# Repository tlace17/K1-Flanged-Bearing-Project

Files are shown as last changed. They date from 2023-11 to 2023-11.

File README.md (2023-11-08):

# K1-Flanged-Bearing-Project
D3D community based K1 and K1 Max Gantry Mod

<table>
  <tr>
   <td colspan="4" >



<p>
The K1 Flanged Bearing Project was developed within the <a href="https://github.com/D3vil-Design">D3vil Design (D3D)</a> community as an effort to further advance the precision and speed of the K1 and K1 Max 3D printers from Creality. Inspired by the work of Derrick Darrell and Omran Al Sayed from the D3D Dev team and their early gantry improvements to the stock setup of the K1 and K1 Max.
<p>
This project aims to replace all idlers on the gantry with the flanged bearing variety commonly seen on Voron Design printers over the last 5 years. These provide improved belt alignment and quieter operation at faster speeds. These bearings alongside some changes to the gantry idler locations provide a proper belt path for standard corexy operation.
<p>
<strong>Included in this document are installation manuals for all 3 types of components within the gantry upgrades and a Bill of Materials for needed parts.</strong>

<h1>Print Settings:</h1>
<p>
<strong>Material:</strong> ABS or better
<p>
<strong>Infill:</strong> Gyroid 20% or more
<p>
<strong>Layer Height:</strong> 0.2mm maximum, 0.12mm preferred
<p>
<strong>Wall Loops:</strong> 2 minimum, 3-4 preferred
<p>
<strong>Top and Bottom Layers:</strong> 4 minimum, 5 preferred
<p>
<strong>Supports:</strong> Needed (Normal is better than tree for most parts, be careful removing supports)
<p>
<h1>Install Manuals:</h1>

<p>
<a href="https://docs.google.com/document/u/0/d/1f634rc0oCE0zsnbUDskOYYNibStS-vbxrUdUEM-Z9eU/edit">Tensioner Assembly</a>
<p>
<a href="https://docs.google.com/document/u/0/d/1OAUH_pnmw2NlV73cRtI84WbWtc6erK8xQ9Lfi24KxoA/edit">Motor Mount Assembly</a>
<p>
<a href="https://docs.google.com/document/u/0/d/13FziAajVrfHMsXNUPVWEJ_OhXhJzXreVzjQ5gYJWXsE/edit">XY Joint Assembly</a>
<h1>BOM</h1>

   </td>
  </tr>
  <tr>
   <td>Count
   </td>
   <td>Item
   </td>
   <td>Amazon
   </td>
   <td>AliExpress
   </td>
  </tr>
  <tr>
   <td>2
   </td>
   <td>M3x20 and/or M3x25 SHCS
   </td>
   <td><a href="https://www.amazon.com/iExcell-Stainless-Metric-Socket-Washers/dp/B0812TYT5L/">https://www.amazon.com/iExcell-Stainless-Metric-Socket-Washers/dp/B0812TYT5L/</a>
   </td>
   <td><a href="https://www.aliexpress.us/item/2251832670224681.html">https://www.aliexpress.us/item/2251832670224681.html</a> <strong>(Select M3)</strong>
   </td>
  </tr>
  <tr>
   <td>6
   </td>
   <td>M3x25 FHCS
   </td>
   <td><a href="https://www.amazon.com/gp/product/B09BRDLF6N/">https://www.amazon.com/gp/product/B09BRDLF6N/</a>
   </td>
   <td><a href="https://www.aliexpress.us/item/3256801607716281.html">https://www.aliexpress.us/item/3256801607716281.html</a> <strong>(Select M3x25)</strong>
   </td>
  </tr>
  <tr>
   <td>18
   </td>
   <td>M3 Heat Set Inserts
   </td>
   <td><a href="https://www.amazon.com/gp/product/B08K1BVGN9">https://www.amazon.com/gp/product/B08K1BVGN9</a>
   </td>
   <td><a href="https://www.aliexpress.us/item/3256804437259312.html">https://www.aliexpress.us/item/3256804437259312.html</a> <strong>(Select M3xOD4.6 +5.5mm length)</strong>
   </td>
  </tr>
  <tr>
   <td>6
   </td>
   <td>M3 Thin Square Nut
   </td>
   <td><a href="https://www.amazon.com/gp/product/B0BD2N9KTV/">https://www.amazon.com/gp/product/B0BD2N9KTV/</a>
   </td>
   <td><a href="https://www.aliexpress.us/item/3256804297147723.html">https://www.aliexpress.us/item/3256804297147723.html</a> <strong>(Select M3)</strong>
   </td>
  </tr>
  <tr>
   <td>24
   </td>
   <td>F623zz Bearings
   </td>
   <td><a href="https://www.amazon.com/dp/B0CGXF7JMP">https://www.amazon.com/dp/B0CGXF7JMP</a>
   </td>
   <td><a href="https://www.aliexpress.us/item/2251832201217481.html">https://www.aliexpress.us/item/2251832201217481.html</a><strong> (Select F623ZZ)</strong>
   </td>
  </tr>
  <tr>
   <td>
   </td>
   <td>or
   </td>
   <td>
   </td>
   <td>
   </td>
  </tr>
  <tr>
   <td>24
   </td>
   <td>F623 2RS Bearings
   </td>
   <td><a href="https://www.amazon.com/dp/B0CGXFY2BX/">https://www.amazon.com/dp/B0CGXFY2BX/</a>
   </td>
   <td><a href="https://www.aliexpress.us/item/2255800912664897.html">https://www.aliexpress.us/item/2255800912664897.html</a>
   </td>
  </tr>
  <tr>
   <td>4
   </td>
   <td>M3x40 FHCS
   </td>
   <td><a href="https://www.amazon.com/gp/product/B09BRDLF6N/">https://www.amazon.com/gp/product/B09BRDLF6N/</a>
   </td>
   <td><a href="https://www.aliexpress.us/item/3256801607716281.html">https://www.aliexpress.us/item/3256801607716281.html</a> <strong>(Select M3x40)</strong>
   </td>
  </tr>
  <tr>
   <td>8
   </td>
   <td>M5x5mm Set Screw
   </td>
   <td><a href="https://www.amazon.com/gp/product/B0BXNL9S4D/">https://www.amazon.com/gp/product/B0BXNL9S4D/</a>
   </td>
   <td><a href="https://www.aliexpress.us/item/3256805120444593.html">https://www.aliexpress.us/item/3256805120444593.html</a>
   </td>
  </tr>
  <tr>
   <td>24
   </td>
   <td>M3 1mm Spacer
   </td>
   <td><a href="https://www.amazon.com/gp/product/B01N7CJMVL/">https://www.amazon.com/gp/product/B01N7CJMVL/</a>
   </td>
   <td><a href="https://www.aliexpress.us/item/3256802114850018.html">https://www.aliexpress.us/item/3256802114850018.html</a> <strong>(Select M3x6xThick + 1mm thick)</strong>
   </td>
  </tr>
  <tr>
   <td>16
   </td>
   <td>M3x8 FHCS
   </td>
   <td><a href="https://www.amazon.com/gp/product/B09BRDLF6N/">https://www.amazon.com/gp/product/B09BRDLF6N/</a>
   </td>
   <td><a href="https://www.aliexpress.us/item/3256801607716281.html">https://www.aliexpress.us/item/3256801607716281.html</a> <strong>(Select M3x8)</strong>
   </td>
  </tr>
    <tr>
   <td>12
   </td>
   <td>M3x0.5 Spacer/Washer
   </td>
   <td><a href="https://www.amazon.com/gp/product/B09BRDLF6N/">https://www.amazon.com/gp/product/B09BRDLF6N/</a>
   </td>
   <td><a href="https://www.aliexpress.us/item/3256802114850018.html">https://www.aliexpress.us/item/3256802114850018.html</a> <strong>(Select M3x6xThick + 0.5mm thick)</strong>
   </td>
  </tr>
</table>

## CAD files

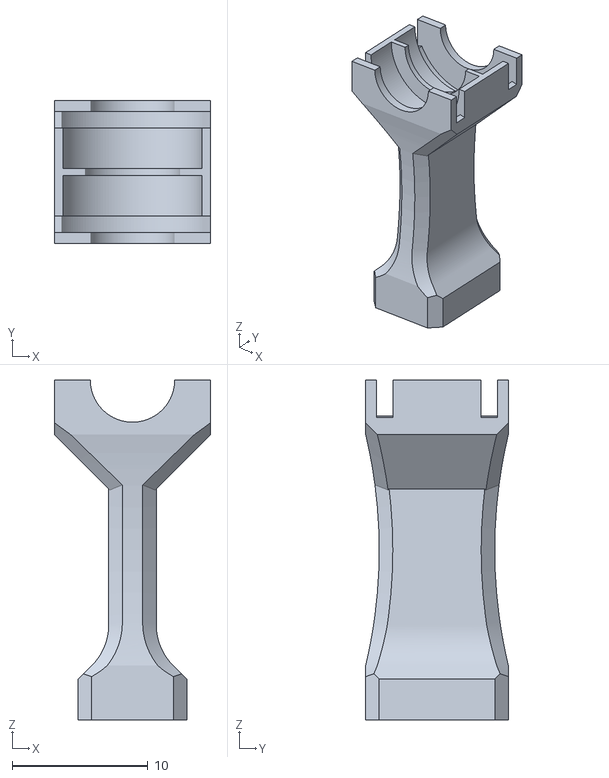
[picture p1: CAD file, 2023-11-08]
Bearing Stack Tool.stl
11.5 x 10.5 x 25.0

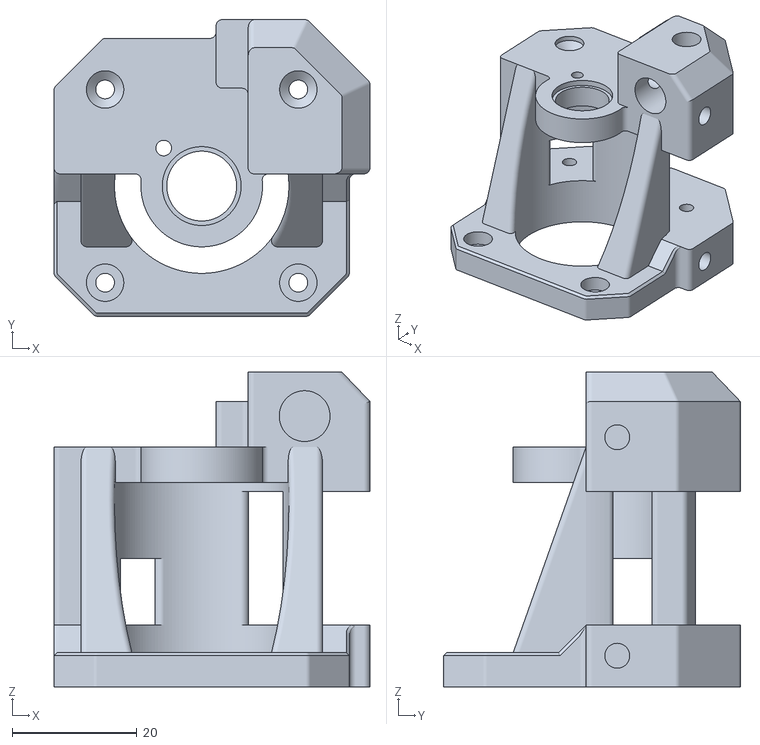
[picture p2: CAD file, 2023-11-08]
Gantry STLs/Right Stepper Mount.stl
50.7 x 47.6 x 50.5

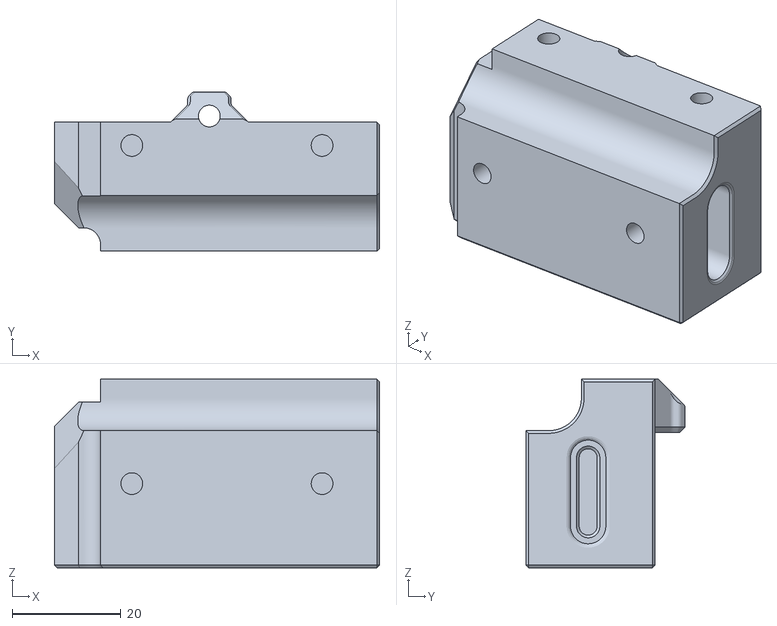
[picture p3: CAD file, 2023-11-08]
Gantry STLs/Left Tensioner Housing.stl
59.9 x 29.4 x 34.8

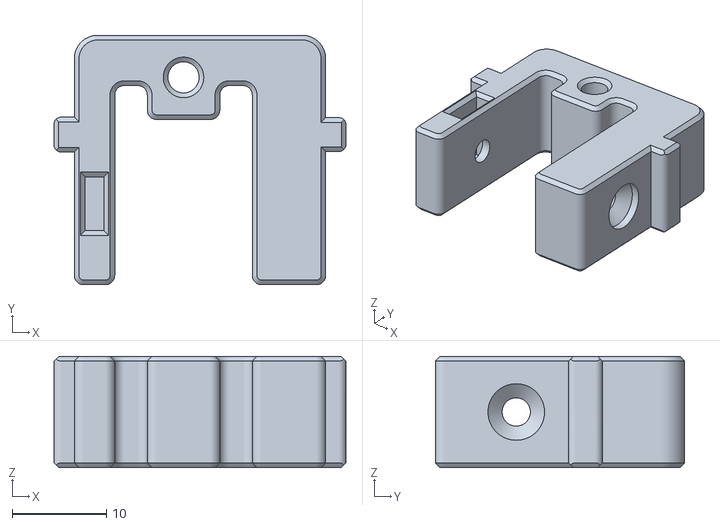
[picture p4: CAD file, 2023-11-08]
Gantry STLs/Left Tensioner.stl
31.0 x 26.5 x 11.8

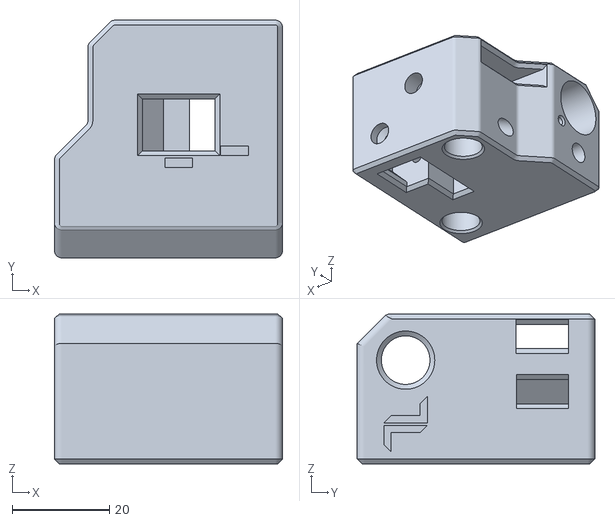
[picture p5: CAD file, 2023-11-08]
Gantry STLs/Right XY Joint.stl
47.0 x 49.0 x 30.9

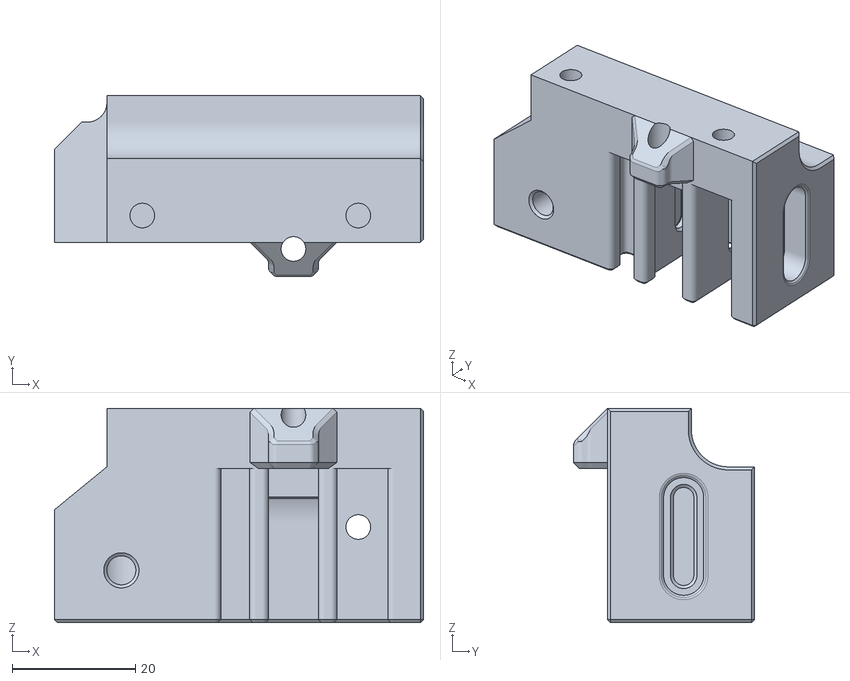
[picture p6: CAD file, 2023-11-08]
Gantry STLs/Right Tensioner Housing.stl
59.9 x 29.4 x 34.8

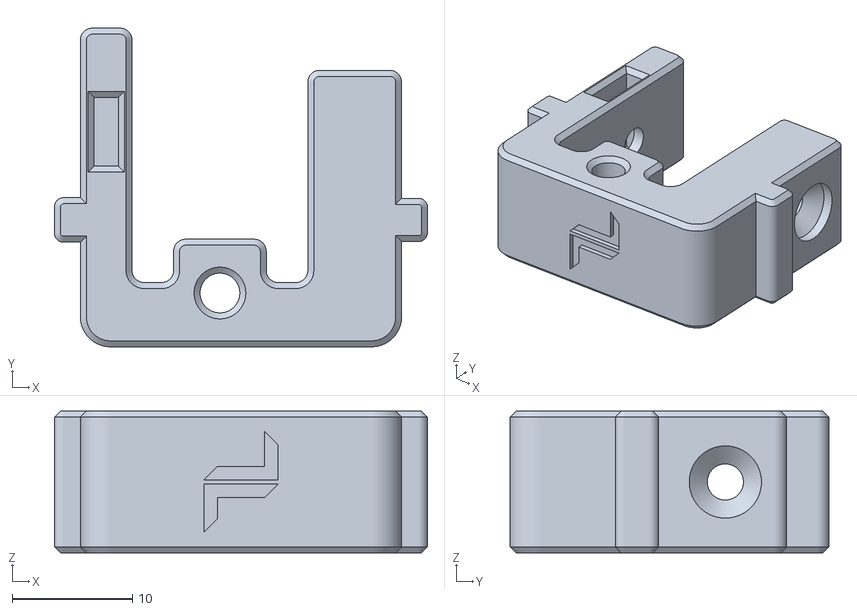
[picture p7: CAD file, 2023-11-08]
Gantry STLs/Right Tensioner.stl
31.0 x 26.5 x 11.8

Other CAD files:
Gantry STLs/Left Stepper Mount.stl
Gantry STLs/Left XY Joint.stl
